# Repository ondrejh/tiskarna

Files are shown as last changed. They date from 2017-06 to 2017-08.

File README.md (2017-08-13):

# 3D Tiskárna

Jak jsem stavel 3d tiskarnu

## Příběh

Rozhodl jsem se postavit (si) 3D tiskárnu. Je toho plný internet a nemůže to být přeci těžké. Jsem programátor, pracuji s krokovými motory a kolegové mají profi tiskárnu, kterou používají denně. Co víc si přát ...

## Výběr modelu (loop)

Tady už jde do tuhého (to brzo). Internet je sice "plný" různých návodů, schématů a sestav, ale má to háček. Vývoj v segmentu je jaksi překotný, návody nedatované a neúplné, a ty lepší obvykle patří k nějakému prodávanému kitu. Né že bych o koupi nějakého neuvažoval, jen mi to přijde moc snadné.

Po prvním průzkumu se mi zdála jako ideální cesta tiskárna typu [reprap mendel](http://reprap.org/wiki/Mendel). Není nad první dojmy ...

Na druhý pohled se mi zdá lepší [reprap huxley](http://reprap.org/wiki/Huxley). Sice je menší, ale víc se toho bude dát vytisknout v práci. Ale ... ale je osazená motory Nema14 - ty já "Nema"ám.

Pro neznalého začátečníka to skutečně není lehká volba. Zkusím tedy štěstí a dám první slušný návod na typ Mendel. Asi [reprappro.com/documentation/mendel-tricolour](https://reprappro.com/documentation/mendel-tricolour/). Na stránkách prodávali i kit, ale ten už k sehnání není. Proč asi? Nevím. Ale zkusím to.

## Rozpočet
* Závitové tyče, matky, podložky .. 196Kč
* Ložiska 608ZZ .. 36Kč
* Matky, podložky (druhé kolo) .. 132Kč (95Kč jsou těsnící podložky - ty tam nepatří)
* MDF desky .. 1034 Kč (mám toho přibližně 100x víc než potřebuju)

* Ložiska 623ZZ 30ks (Aliexpress) .. 3.00$
* Ložiska LM8UU 24ks (Aliexpress) .. 12.00$
* Řemínek GT2 6mm 10m (Aliexpress) .. 7.99$
* Řemenička GT2 16zubů 5ks (Aliexpress) .. 3.30$
* Heatbed MK2B 1ks (Aliexpress) .. 8.37$
* Řídící deska Melzi 2.0 1ks (DealExtreme) .. 26.11$

* Celkem (zatím) .. 1398 Kč, 55.77$ (1264 Kč)

## Build log

### Pondělí 19.6.
Procházím DXko a podobné "číňany", co se dá koupit. Zatím objednávám jen řídící desku - je to trochu předčasné, ale mám strach, že byh jí příště nenašel. Link přidám později (TODO)

### Úterý 20.6.
V železářství kupuju 7 metrových závitových tyčí M8 a matky s vějířovými podložkami - cca 200kč. Hlazenky nemají (zatím). Na ložiska se zeptám v práci - update (21.6.): prý je mají v kšeftu se zahradní technikou.

### Středa 21.6.
Čeká mě první "na zkoušku" vytisknutý díl. Jde o držák motoru osy Z - patří do [konstrukce rámu](https://reprappro.com/documentation/mendel-tricolour/frame-assembly/). Vypadá dobře, nemůžu se dočkat na další.

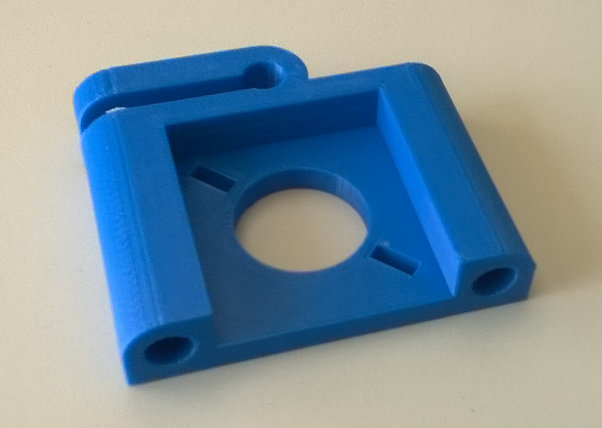
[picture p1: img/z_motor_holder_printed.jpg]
z_motor_holder_printed


Znovu procházím návod a zjišťuju, že závitových tyčí M8 bude potřeba asi jen 6. Ta sedmá je M5 pohonu osy.

### Čtvrtek 22.6.
Čekání na díly ... to může trvat věčnost, než se na tiskárně dostanu na řadu. Zatím jsem alespoň naporcoval závitovinu. Opravil jsem si na to starou stolní úhlovou rozbušovačku. Navařil jsem jí kolečka a madlo, aby se dala líp přemísťovat a vyměnil jí kabel a koncovu na nový 16A pětíkolík. Nakrátil jsem na ní dvě tyčky a zbytek jsem dodělal pilkou na železo a pilníkem. Flexa to prostě moc ubírá, řeže na hrubo, pálí pozink, a ani zabroušení není to pravé, takže se pak musí opravovat závit. Někdy jsou prostě lepší jednoduché nástroje...

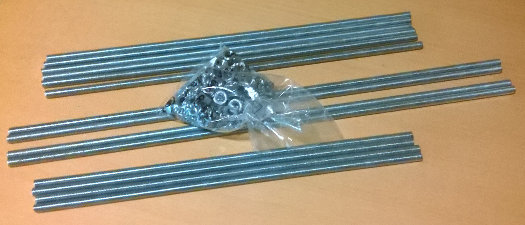
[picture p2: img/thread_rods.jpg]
thread rods, nuts and lock washers


Zdá se, že hlazenky mi zajistí Brašule. Dokonce na míru. A ložiska asi taky (update - ložiska ne, takový nemají - jako u nás). Nechápe, proč jsem to neřekl hned. Závitoviny mají taky kupu. Hold, líná huba holý neštěstí :smile:

### Pátek 23.6.
Tištěné díly framu jsou hotové (asi protekce, nebo co). Ložiska vezmu cestou z práce v tom [kšeftu se sekačkama](www.agrico-sro.cz). Hlazenky budou večer u Brašuleho. Můžu skládat.

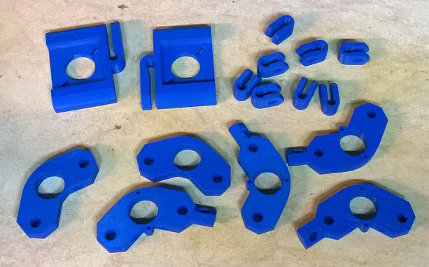
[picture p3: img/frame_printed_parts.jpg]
frame printed parts


Postup přesně podle [návodu](https://reprappro.com/documentation/mendel-tricolour/frame-assembly/). Při montáži trojůhelníků je potřeba zkontrolovat aby byly nohy proti sobě - to je i v návodu zdůrazněno. Nevšiml jsem si ale, že by tam bylo zdůrazněno, že je na totéž potřeba dát pozor, když se trojůhelníky sesazují na příčníky. Takže jsem to dělal dvakrát.

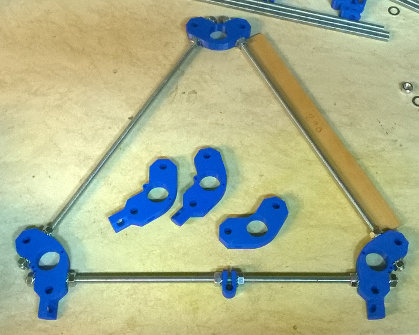
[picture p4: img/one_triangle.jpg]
triangle assembling

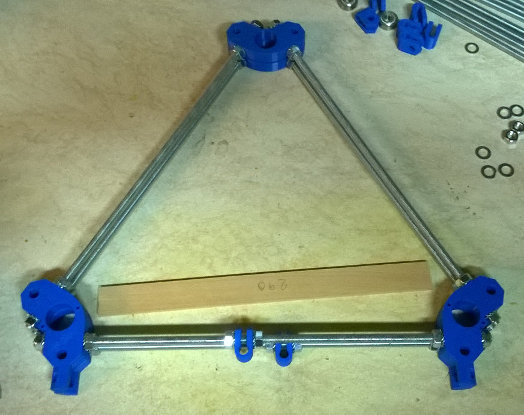
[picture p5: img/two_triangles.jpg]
triangles ready


Příprava příčníků. V tomhle návodu nic moc. Je tam sice textové schéma "nut,washer,nut ..." ale v tom se dá snadno ztratit. Na [www.reprap.org](http://www.reprap.org/) jsem viděl i pěkné [grafické schéma](http://reprap.org/wiki/File:Rear-rods.png). Ale nakonec i podle tohohle se to dá.

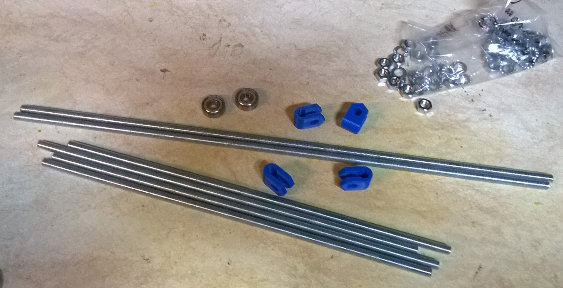
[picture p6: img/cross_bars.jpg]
cross bars

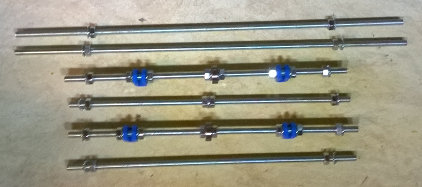
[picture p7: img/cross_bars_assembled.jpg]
cross bars assembled


Tak, A došly mi matky a podložky. Nějak jsem si špatně prošel návod a špatně jsem to sečetl. Myslel jsem, že budu potřebovat něco málo přez 50ks, tak jsem vzal 60. A jsou pryč a ještě zdaleka nejsem u konce. Ach jo ... Dnes už je nikde nekoupím. Takže pro dnešek konec.

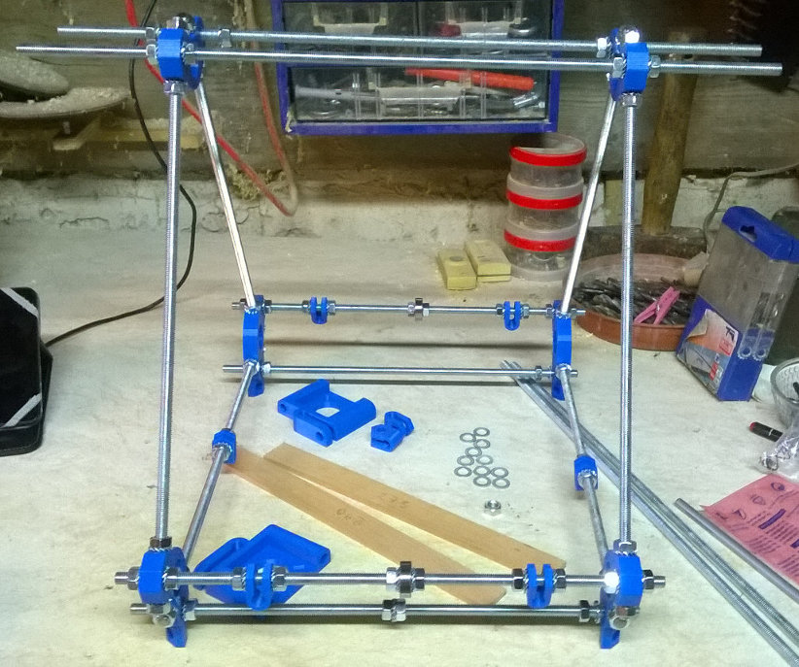
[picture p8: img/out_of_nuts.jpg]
cant continue .. out of nuts


Jo, abych nezapomněl. Ty hlazenky. Takhle já to s ním mám. Když chci něco po dvou kusech, dodá toho dvě sady. Asi se mu s jednou nechtělo dělat. Díky Brašule :smile:

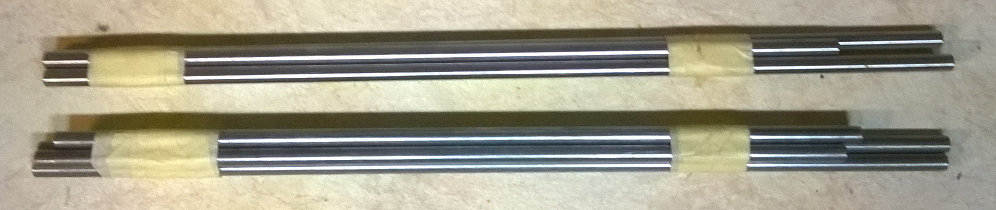
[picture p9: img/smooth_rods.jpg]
smooth rods - two sets


### Sobota 24.6.
Ráno jsem dokoupil potřebný spojovací materiál. Sehnal jsem dokonce i MDF desky - měl jsem obavu, že je ani nebudou mít. Ale o tom později.

Teď mám hotový a seřízený rám. V tomto bodě je návod trochu nejednoznačný a přeházený, ale v principu to funguje. Nevím jestli jsem měl takové štěstí, nebo jestli jsem tak dobře měřil, ale všechno sedí. Osa Y je vodorovná a souosá (test se sklem) a osa Z je kolmá, souosá a seřízená na střed osy Y (je to hlavně práce s úhelnicí). Chce to od začátku stavět na klalitní vodorovné podložce - třeba silna kuchyňská deska je OK.

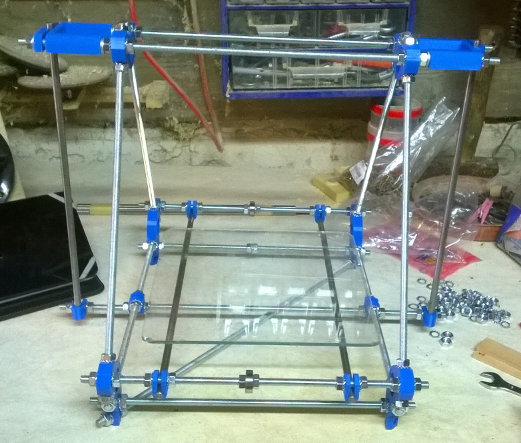
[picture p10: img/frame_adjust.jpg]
Y axis adjustment


Dodávám ještě přehled použitého nářadí: Sklo, nebo jiná plochá tuhá věc na kontrolu osy Y. Kvalitní úhelnice. Laťky - těmi jsem vytvořil spojnici mezi hlazenkami osy Z, abych ji ustavil na střed osy Y - v návodu se používa provázek, nebo gumička - to se mi moc nezdálo. Z jiného kusu stené laťky jsem si vyrobil takové měrky "templaty". V kitu by měl být přiložený takový vypálený hřebínek, ale já ho samozřejmě nemám. Možná si ho taky nechám vypálit - pro zajímavost. Nějaký metr. Fixa - ta se pořád válí na stole. No a 13ka klíč - asi na ďoubání v nose, nééé :smile:

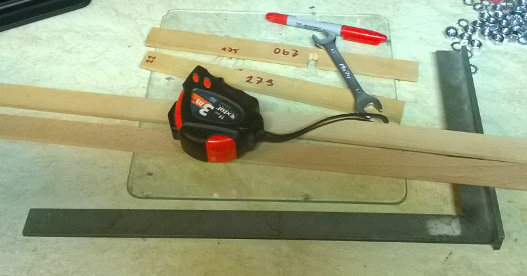
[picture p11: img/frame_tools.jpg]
Frame tools


Zpátky k těm MDFkám. Mají je v Trutnově v [DřevoTrust](http://www.drevotrust.cz/cz/). Ochotně je i nařežou, což je potřeba, protože prodávají jen po celých deskách. Cca 2x3m. No, vzhledem k tomu, že budu potřebovat tak A4 (odhad), tak mi asi něco zbyde. Alespoň se mi nestane to co s matkami.

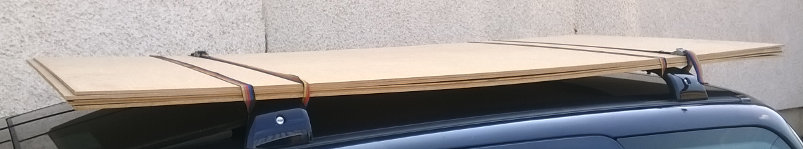
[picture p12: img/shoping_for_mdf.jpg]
MDF shopping


Teď začne skutečné shánění. CNC laser, miniaturní a lineární ložiska, řemínek a řemeničky (GT2) aj. Počítám, že už to tak hladce nepůjde. Ale o to ani nešlo ...

### Pondělí 26.6.
Dnes jsem se domluvil se švárou, že mi vypálí díly z MDF desek. Maximální formát, který se vejde do jeho laseru je A3plus. Třetinu desek jsem tedy podle toho připravil.

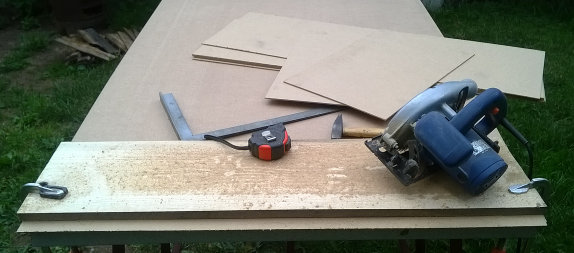
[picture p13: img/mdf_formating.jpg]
MDF formating

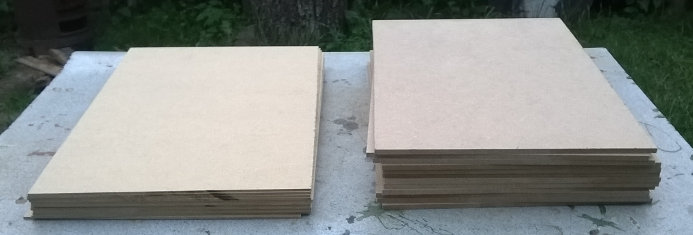
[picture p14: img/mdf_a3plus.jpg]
MDF_a3plus


Teď mám tedy po 12ti kusech polotovaru od každé tlouštky a ještě dvě třetiny materiálu na půdě.

Ještě musím připravit podklady. V originálech na githubu se bohužel počítá s větší plochou laseru.

### Středa 28.6.
Dnes jsem připravil podklady pro laserování. Zítra ráno jdeme na to.

### Čtvrtek 29.6.
Díly jsou vypálené. Nešlo to zas tak hladce, ale dobrá zpráva je, že to jde i z DXF a propálí to i tu 6mm desku (ale na dvakrát). Cesta je ale prošlápnutá - příště to půjde snáz. Díky [šváro](http://www.razitkanachod.cz/)!

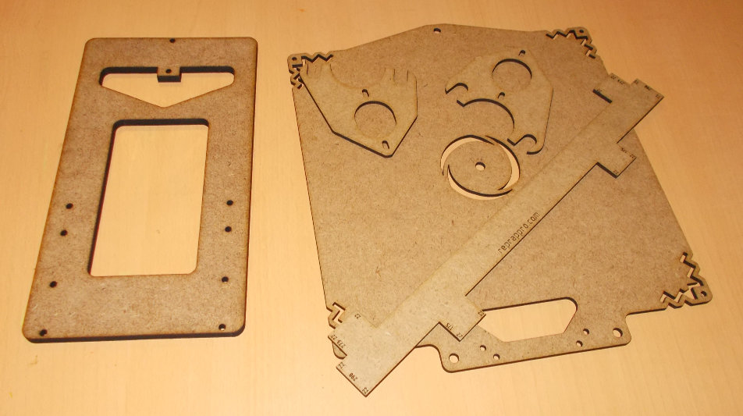
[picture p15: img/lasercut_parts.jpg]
Lasercut parts


Do tisku jdou díly na osu Y.

### Pátek 30.6.
Díly jsou vytisknuté, ale ty složitější nejsou ještě vylouhované. No nevadí, stejně nemám ložiska ani řemínek.

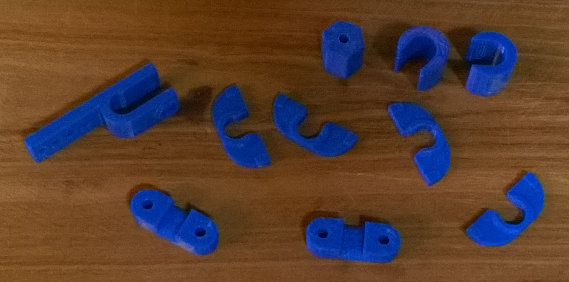
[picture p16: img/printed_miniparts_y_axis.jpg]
Printed parts Y axis - some of them


### Sobota 1.7.
Nějak jsem to nevydržel a sestavil jsem si alespoň držák motoru. I když bez mikro-ložisek a bez řemeničky.

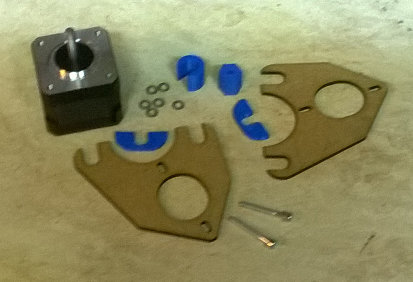
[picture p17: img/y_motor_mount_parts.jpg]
Y motor mount parts (no bearings)

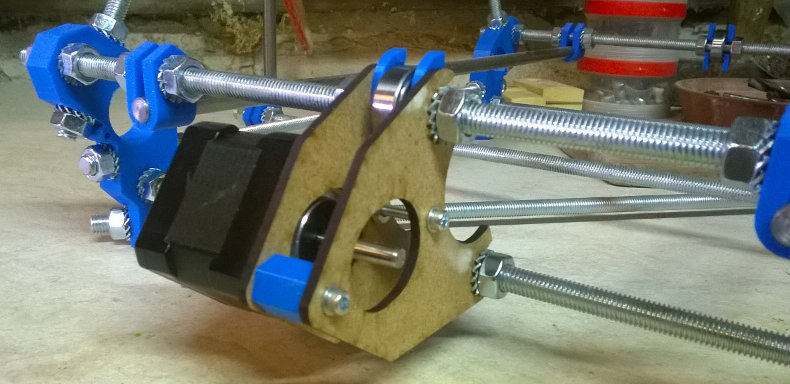
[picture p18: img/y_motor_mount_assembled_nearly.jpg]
Y motor mount assembled (no bearings and puley)


### Pondělí 3.7.
Dostal jsem "důkladně" vylouhované zbylé tištěné díly osy Y. Zatím ale stále nemám ložiska.

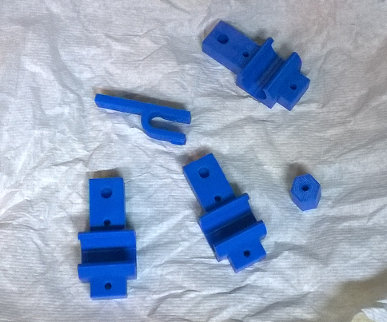
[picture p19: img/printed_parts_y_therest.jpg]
Printed parts Y axis - the rest of them


### Úterý 4.7.
Alespoň nasladko to sestavím...

Frog parts - no bearings

Taková drobnost: Montážní díry d5mm s osazením pro matku v držáku "žáby" jsou zarostlé tenkou šlupkou a musejí se odvrtat. Kluci v práci tvrdí, že to je chyba v ".STL". Odvrtat to jde snadno a strukturu to nenaruší.
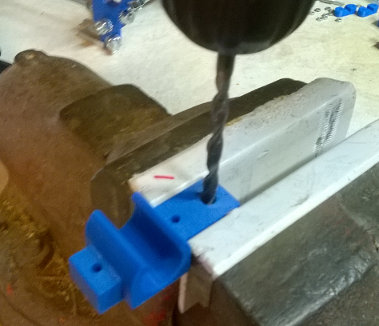
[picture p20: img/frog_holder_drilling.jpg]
Frog holder drilling


Druhá poznámka: Jsou předepsané šrouby M3x25mm s imbusovou hlavou. Těch 25mm to je HOODNĚ velká rezerva. Řekl bych že 20mm by bohatě stačilo. Navíc né v každém železářství mají pojistné matky M3 - to jsou opravdu blechy - takže zatím dávám normální (mám jich kupu).
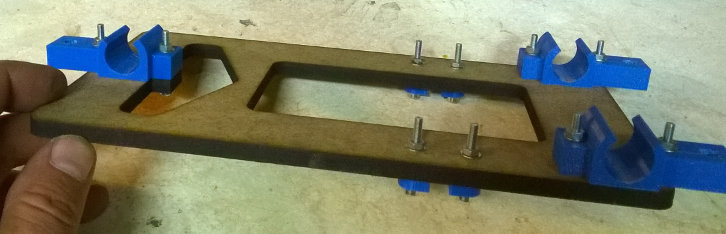
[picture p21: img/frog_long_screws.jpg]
Frog - long screws


No ... zatím asi takhle:
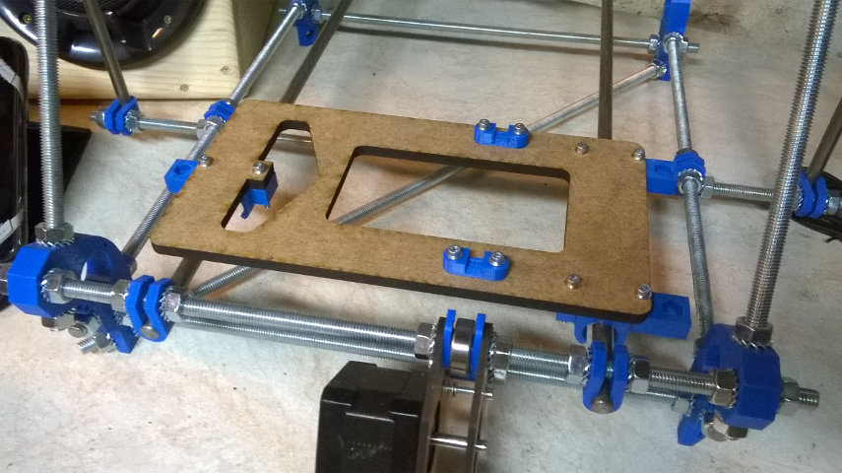
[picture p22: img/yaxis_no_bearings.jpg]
Y axis no bearings


Sice jsou ložiska a řemínky už nějaký týden na cestě z Číny, ale asi si je objednám někde u nás. Prostě se mi nechce čekat.

### Čtvrtek 13.7.
Ložiska, řemínky, řemeničky, řídící deska a dokonce i headbed jsou stále na cestě. Nechal jsem si zatím vytisknout díly na osu X a nakrátit hlazenky. Bohužel došel obyč materiál, takže jsou z nerezi. Jsem zvědav co na to budou říkat ložiska. Nevím jak se mi mohlo stát, že jsem na tyhle tyčky posledně zapomněl.
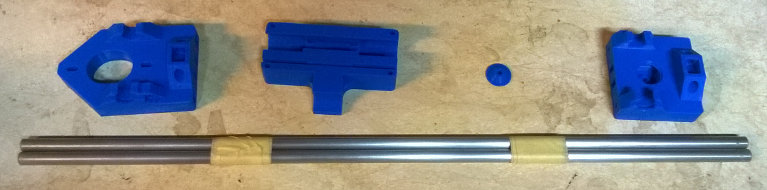
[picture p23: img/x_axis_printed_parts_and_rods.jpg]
X axis printed parts and rods


### Úterý 18.7.
Přišly díly z Číny. Ložiska LM8UU, ložiska 623, řemínek, řemeničky a řídící deska.
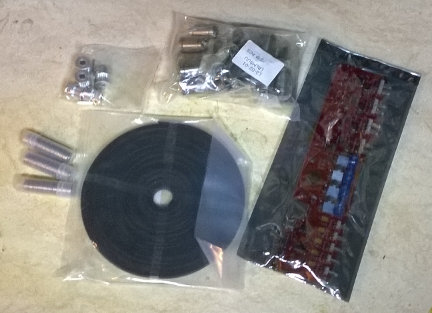
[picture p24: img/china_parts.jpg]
Parts from China


### Středa 19.7.
Nemám moc čas, tak alespoň na večer (v noci) skládám osu Y - doplňuju o ložiska a řemen. Mám trochu pocit, že jsem ho přepnul. Uvidíme až se to bude mět hýbat. Řemínku jsem koupil 10m, ale přesto jsem ho chtěl šetřit - bude se hodit. Takže jsem musel podle návodu po připevnění první svorky protahovat celou délku všemi průvlaky na tiskárně. Připadal jsem si, jako když se snažím namotat sežvýkanou videokazetu (pro pamětníky).
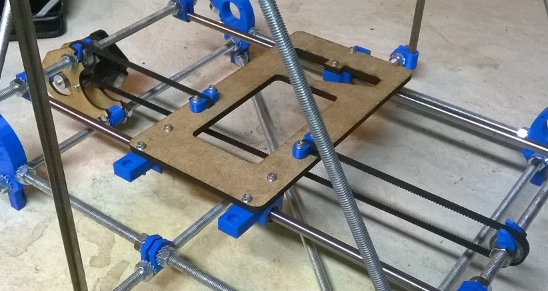
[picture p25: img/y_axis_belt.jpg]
Y axis belt and bearings


Ale jezdí to pěkně. Tím je hotová [osa Y](https://reprappro.com/documentation/mendel-tricolour/y-axis-assembly/) - tedy kromě koncáku. Už se těším až to zkusím rozhýbat. Škoda, že nemám víc času. Jo, mimochodem. Dnes přišel ještě jeden balík - heatbed - no ten si ještě počká.

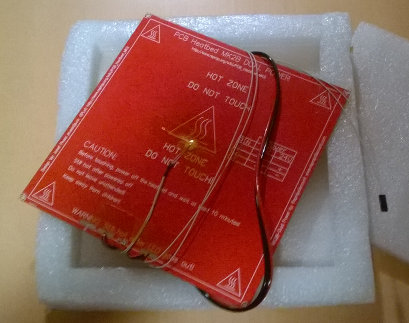
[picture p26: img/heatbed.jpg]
Heatbed package


### Pondělí 24.7.
Poskládal jsem osu X. Chybí mi jen koncák - stejně jako u osy Y - a budu mít hotový [další krok](https://reprappro.com/documentation/mendel-tricolour/x-axis-assembly/).

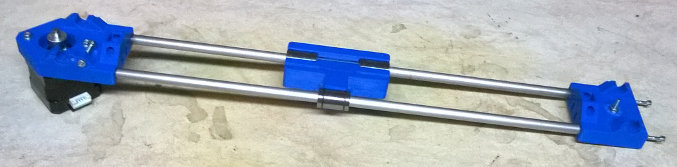
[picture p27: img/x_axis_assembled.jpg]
X axis assembled


Ty koncáky určitě seženu. Horší ale bude sehnat futýrka na osu Z. Vážně nevím, kde to koupit. Asi zkusím přemluvit bráchu, aby mě je vystrouhnul z mosazi.

### Neděle 13.8.
Před dovolenou mi kluci vytiskli spony na osu Z, sehnal jsem nějaké pružinky a šrouby co jsem ještě neměl a dokonce jsem přez dealera Igusu v práci sehnal i ty futýrka (doplnit typ). Abych se nenudil. Teď mám po dovolené a ani sem na to nesáhnul ... klasika. Snad večer.

pokračování příště ...

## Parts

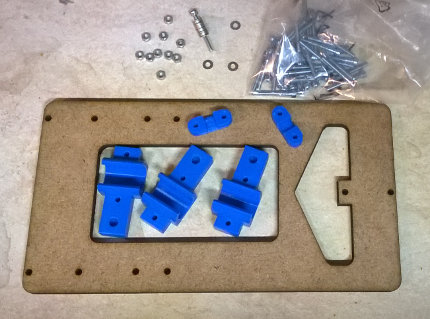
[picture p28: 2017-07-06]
img/yaxis_parts_nobearing.jpg

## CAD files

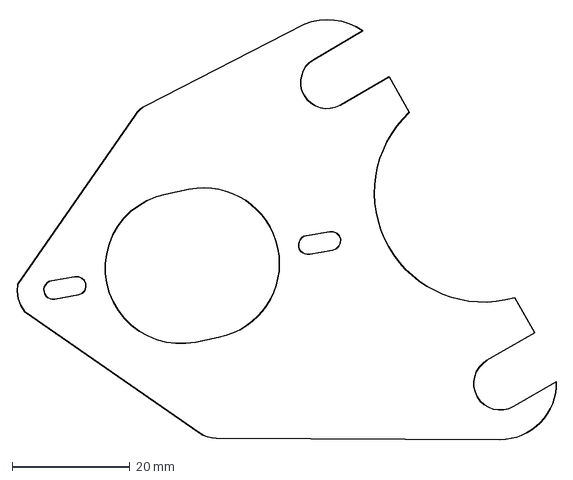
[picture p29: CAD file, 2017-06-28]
lasercut/Y-Motor-Bracket.DXF
91.6 x 71.7 mm

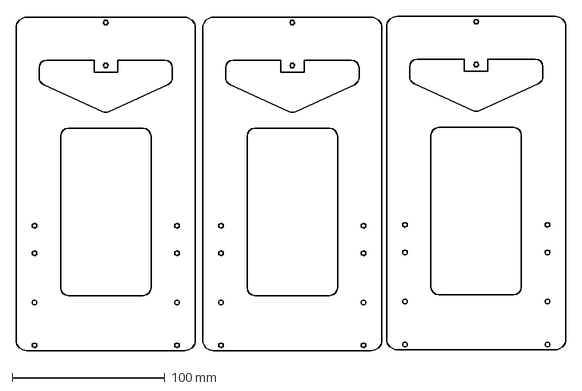
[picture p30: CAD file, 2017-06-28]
lasercut/A3_6mm_sheet.dxf
359.4 x 218.6 mm

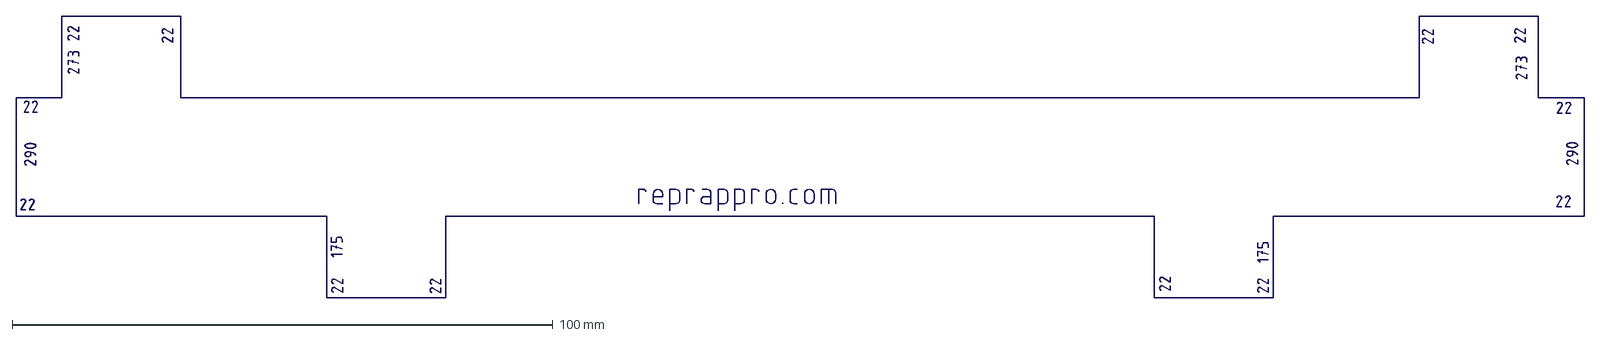
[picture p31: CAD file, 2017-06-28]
lasercut/length-measuring-jig.dxf
290.0 x 52.0 mm

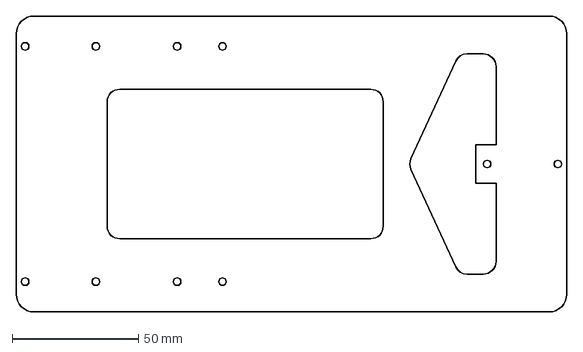
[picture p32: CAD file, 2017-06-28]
lasercut/Y-frog.DXF
218.0 x 117.2 mm

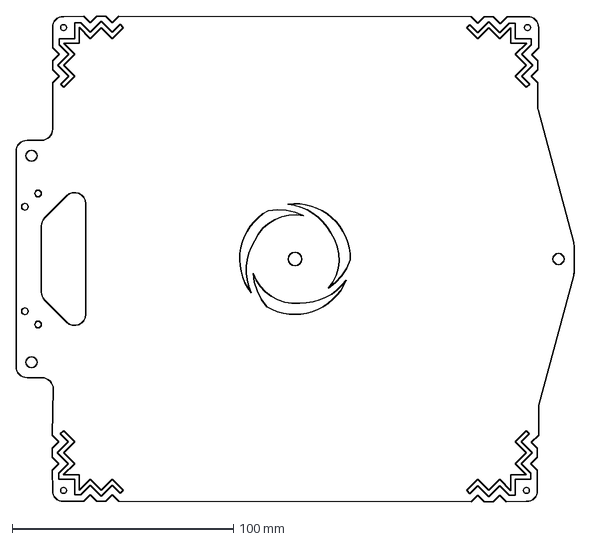
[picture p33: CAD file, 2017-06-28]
lasercut/heatbed-insulator.DXF
252.0 x 219.3 mm

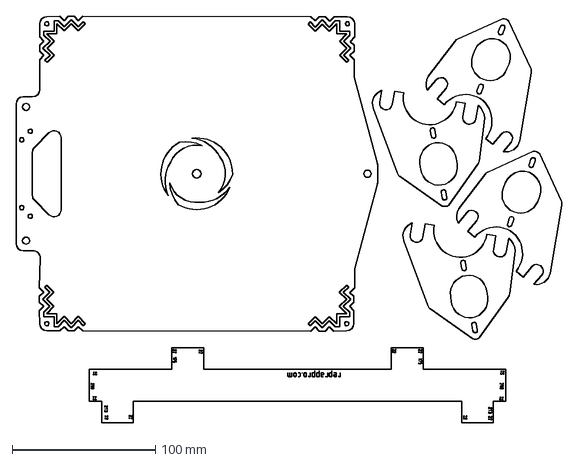
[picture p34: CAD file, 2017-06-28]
lasercut/A3_3mm_sheet.dxf
380.6 x 283.0 mm

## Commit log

2017-06-21 frame assembly link
2017-06-22 no bearings
2017-06-23 thread rods img
2017-06-23 frame assembly started
2017-06-24 frame finished
2017-06-28 3mm A3 sheet
    [A3_3mm_sheet.dxf]
2017-06-28 lasercut drawings
    [A3_6mm_sheet.dxf, Y-Motor-Bracket.DXF, Y-frog.DXF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]
2017-06-28 lasercut log
2017-07-01 y motor mount
2017-07-06 frog assembly
2017-07-20 x axis parts
2017-07-20 y belt and bearings
2017-07-20 heatbed package
2017-07-24 x axis assembly
